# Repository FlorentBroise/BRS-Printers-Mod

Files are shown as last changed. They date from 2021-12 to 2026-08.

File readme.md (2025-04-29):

# Welcome to the BRS-Engineering printers upgrades project!


**What is done here?**  The main objective here is to develop relevants upgrades to push the 3D printer to the limit we choose to, especially repetability and high precision quality goals in mind. You will find some manuals, procedures and tips!
Here a lot of premium upgrades for the Vcore3, with a lot of capabilities. Either you can make it yourself, I offer a print service at https://store.brs-engineering.com specialize in PACF materials if needed. Happy browsing!

# Vcore 3.0/3.1/4.0 based
## Quick Navigation

Chapter|Content Description
:---: |-------------------
Intro.|[What is done here?](/intro.md)
1.|[Define what you need](/defineneeds.md)
2.|[Frame](/frame.md)
3.|[General Upgrades and options (Z-Upgrade, AWD,...)](/componentselection.md)
4.|[BOM](/purchased.md)
5.|[L3VER Tensionner / Enclosure Plates / Prototypes](/products.md)
6.|[Assembly Instructions](/assembly.md)
7.|[Klipper Setup](/Klipper/start-table.md)
8.|[Calibration](/calibration.md)
9.|[Procedures](/procedures.md)
10.|[Cura tips](/software.md)
11.|[EVA Mods](/evamods.md)
12.|[VZ Mods](/vzmods.md)
13.|[Spool system)](/options.md)
14.|[How to Print your Parts](/howtoprint.md)
15.|[LEGACY/DEPRECATED](/deprecated.md)
16.|[Usefull links](/links.md)
17.|[Credits](/credits.md)
18.|[CAD changelogs](/changelogs.md)

# BRS-Vulcain I
## Quick Navigation
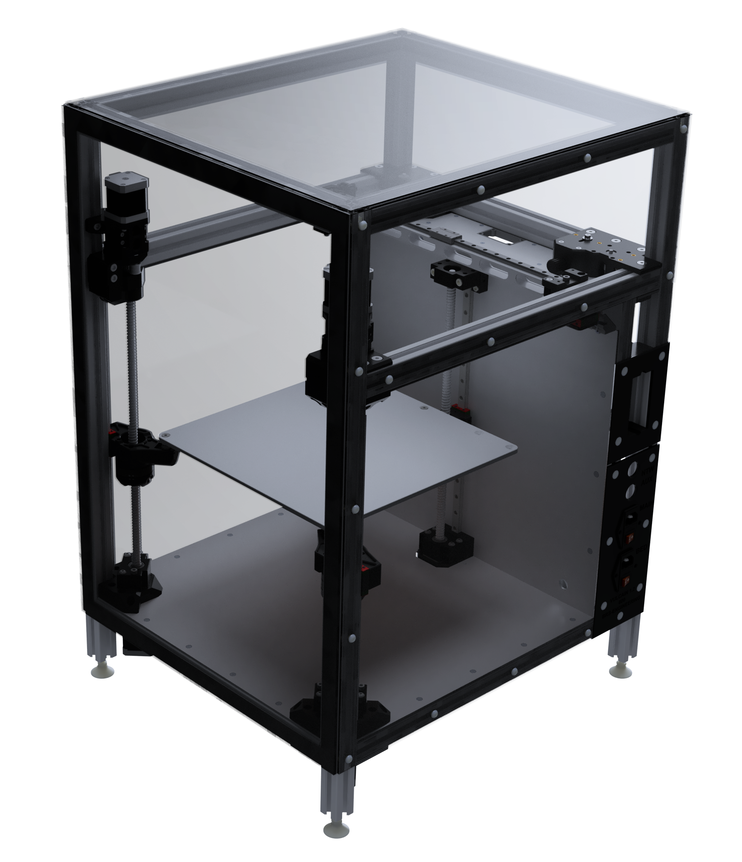
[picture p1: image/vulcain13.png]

Chapter|Content Description
 :---: |-------------------
Intro.|[What is it?](/intro1.md)
1.|[Frame](/frame.md)
2.|[CAD](cad/VULACIN-1.3/Vulcain.md) AVAILABLE

# Licenses

Most projects and designs are licensed as
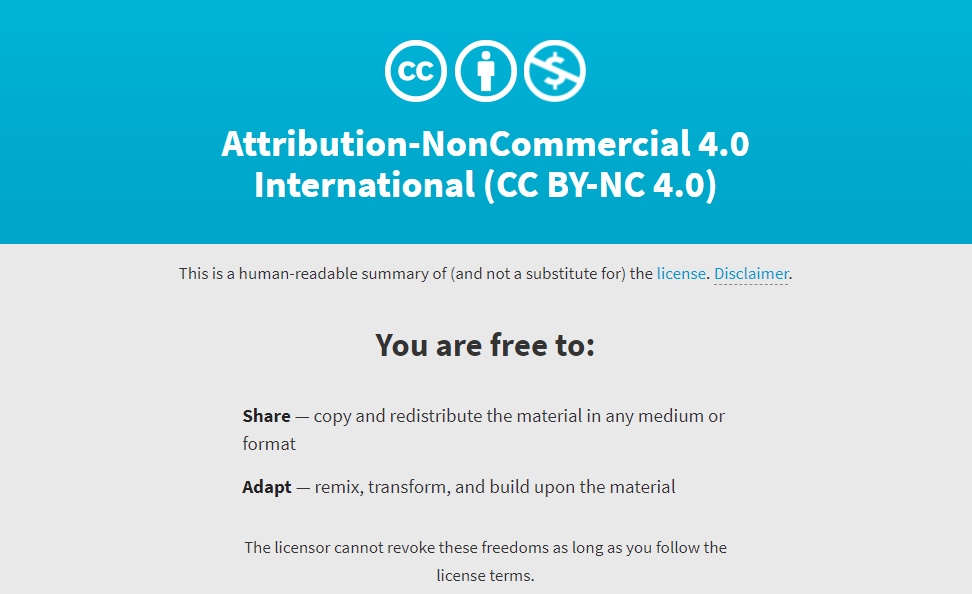
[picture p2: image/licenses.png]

For others, the licence and attribution will be displayed

Feel free to ask if you want to sell it yourself

# Donation

If you like my work and would like to help me covering the costs associated to the development of prototypes and improvements of every projects, my company is a little french one man handed thing ;) <br>
click the button here below :)
[Paypal Donation](https://www.paypal.com/donate/?hosted_button_id=VEMAB3WH74FW2)

# Links

Official Website: https://www.brs-engineering.com/
Official Store: https://store.brs-engineering.com/
Facebook pages: https://www.facebook.com/FlorentBroiseEngineering
Youtube: https://www.youtube.com/channel/UCkiClJtaGl32GyRtkntkpkw

Thank you!
Florent Broise

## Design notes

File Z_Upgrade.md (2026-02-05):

## -/ Z SYSTEM 3.0 (For Vcore 4)

# -/ Z-Upgrade 1204/1605 4.0

A Z-Upgrade complete overhaul for VCORE 4.0/4.1
The Z-Upgrade replace the original Z system with a ballscrews driven system.
More precise, more reliable over time, it offers a very high repeatability and a perfect consistancy in layer staking compared to a trapezoidal screw.
Maintenance-free and made to last in a production line. No wobble over Z.
Proofed design since 2021. More than 450+ happy users

Lifetime support and warranty over the parts

Integrated design pushed further to maximize fonctions and size to keep the whole print Z volume
Following the feedbacks, tests, assemblies, this version is born to simplify, and solve all the little things from the 3.x versions.
Parts count reduced, hardware quantity reduced, steps of assembly reduced, price reduced!

Version|Description|ReleaseDate|CAD|Printable|BOM|Documentation|License|Order
-------------|-----------|-----------|-----------|------------|------------|----------|-----------|-----------
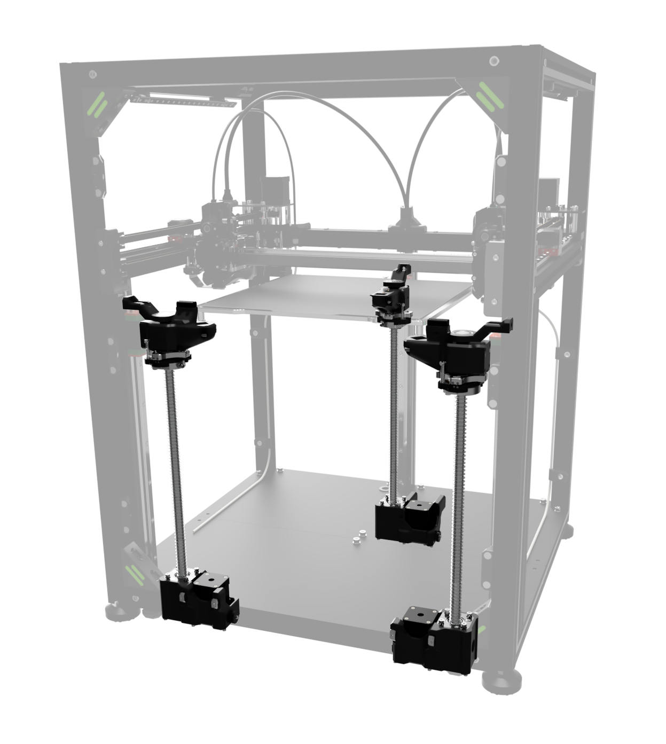
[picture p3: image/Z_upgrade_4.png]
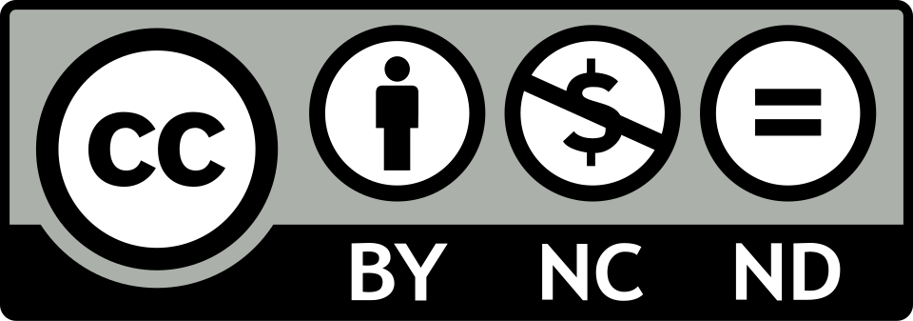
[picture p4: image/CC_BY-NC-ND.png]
**V4.0a 1605 ACTIVE|<br>SFU1605 Version - Release |01/02/26| > | [Files](https://www.printables.com/model/1577140-z-upgrade-40-for-vcore-4041)| [BOM](https://docs.google.com/spreadsheets/d/1dxGWueJq1Y-2fWoLZl0RPUSDvyyU8gKnJiP1dbby-7s/edit?usp=sharing) | [MANUAL](/manuals/Z-Upgrade-4.0-Manual.pdf) || [SHOP on the Store](https://store.brs-engineering.com/products/z-upgrade-4-0-for-vcore-4-0-4-1)

# -/ Z-Upgrade 1204/1605 3.0

Adaptation of the production grade "Z-Upgrade" for VCORE 4.0
Upgrade to replace the original Z with a ballscrew system.
More precise, very reliable over time, offers a very high repeatability in the Z movement compared to a trapezoidal screw.
Maintenance-free*. Made to last in a production line. No wobble over Z. Proofed design over 2021. More than 350+ users since 2021.
A Reinforced version of the 1605 is available too for heavy duty projects. This system has virtually no Z limitations in size, you can dream of the best you can pick ;)

A lot of things has been reworked on this iteration compare to the previous Z-Upgrade 2.0:

-Simplification of parts list, easier implementation. direct bolt in upgrade.

-Directly bolted to the VCORE 4.0 frame and underplate. Re-use the Stock VC4 top retainers (1204 version) + bearings.

-No need of surelevation; the Stock VC4 feet will only need to be adjusted to the height. (+17mm)

-Compatible natively with Wobble X, Oldham V3 proofed printed rings compatible too

-Dense integration of the Oldham/Wobble X in the Arms

-Motor reduction for a very high holding torque, even when the motor aren't active. Proofed for heavy custom bed, or bigger custom print volume machines. Vcore 500 can now run standard Nema 17 without risks of fall when the motor are powered off

-Motor reduction + ballscrew allowing an insane precision over the Z-Motion, extreme constistency, allow thin and repetable layer over time

-No maintenance needed (cleaning+thin lubrication once a year is enough)

-Z-motors easy tension over the 6mm timing belt with 1x M5 screw

-Add +10mm of Z distance (Oldham V3), or +15mm with Wobble X

-All included, no self soucing to do.

[GUIDE TO CHOOSE and PATCH NOTE](https://github.com/FlorentBroise/BRS-Printers-Mod/blob/main/manuals/Z-Upgrade-3.2C-Variants.pdf)

Version|Description|ReleaseDate|CAD|Printable|BOM|Documentation|License|Order
-------------|-----------|-----------|-----------|------------|------------|----------|-----------|-----------
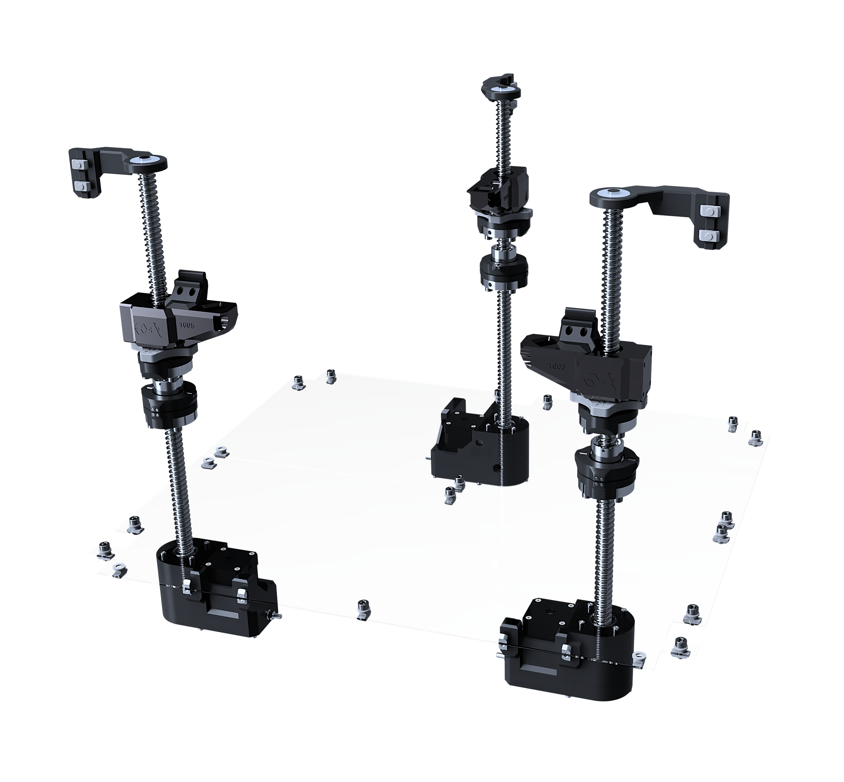
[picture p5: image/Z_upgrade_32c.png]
**V3.0a 1204 DEPRECATED|<br>SFU1204 Version - This version is made to simplify the integration to a stock VCORE 4 (All versions), By taking the same footprint that the stock VCORE 4 parts. You can then use the stock bottom panel you already have, and (PRECISE BOM listed bellow). NO NEED for clearance bellow the frame, tuning the stock Z feet height is enough!. This version keep the same Z volume (+10-15mm bonus) than the stock machine|30/04/24| > |  | [BOM](https://docs.google.com/spreadsheets/d/1E3s1GYlrxwITHgYWx6jKaRsaI9jWW35iHJ5XEkeNflE/edit?gid=0#gid=0) | [MANUAL](/manuals/Z-Upgrade-3.0-Manual-1.0.pdf) ||/
**V3.1a/b 1204 DEPRECATED|<br>SFU1204 + SFU1605 added. - This version is made to implement 1605 version (b) and to change all bottop plate screws to m3x20mm to simplify sourcing|12/11/24| > |  | [BOM](https://docs.google.com/spreadsheets/d/1E3s1GYlrxwITHgYWx6jKaRsaI9jWW35iHJ5XEkeNflE/edit?gid=0#gid=0) | [MANUAL](/manuals/Z-Upgrade-3.0-Manual-1.0.pdf) ||/
**V3.2c 1204/1605 DEPRECATED|<br>SFU1605/SFU1204 Version - This version is made to simplify the production and manufacturing on the BRS side, it merges the 1605 and 1204 designs to count less parts, StarLock design created, some adjustments made on the general design [Z-Upgrade 3.2 PATCHNOTE.pdf](https://github.com/user-attachments/files/17843025/Z-Upgrade.3.2.PATCHNOTE.pdf)|21/01/25| > | [1605 STL-STEP-F3z](https://www.printables.com/model/1033344-z-upgrade-32-for-vcore-40-sfu1605-sfu1204) [1204 STL-STEP-F3z](https://www.printables.com/model/1419210-z-upgrade-32d-sfu1204-arm-kit) | [BOM](https://docs.google.com/spreadsheets/d/1E3s1GYlrxwITHgYWx6jKaRsaI9jWW35iHJ5XEkeNflE/edit?gid=0#gid=0) | [MANUAL](/manuals/Z-Upgrade-3.0-Manual-1.0.pdf) ||[SHOP ](https://store.brs-engineering.com/products/z-upgrade-3-0-sfu1605-vcore-4-0)
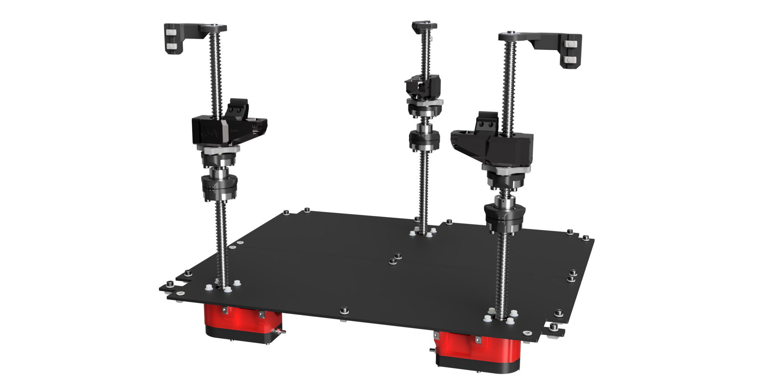
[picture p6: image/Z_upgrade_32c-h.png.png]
**V3.2c-H 1605 ADEPRECATED|<br>SFU1605 Version - This is the Z-Upgrade 3.2C-H iteration (H, for heavy), It answers the need to make a very tall printer (800-1500mm)|17/03/25| > | [STL-STEP-F3z](https://www.printables.com/model/1233695-z-upgrade-32c-h-for-tall-vcore-40-sfu1605) | BOM In progress | [MANUAL](/manuals/Z-Upgrade-3.0-Manual-1.0.pdf) ||[SHOP ](https://store.brs-engineering.com/products/z-upgrade-3-2c-sfu1605-reinforcedvcore-4-0)
**V3.2d 1204/1605 DEPRECATED|<br>SFU1605/SFU1204 Version - Upgrade or the arm design with retaining spings to secure the wobble assembly na dprevent accident or ball bearing drops [Z-Upgrade 3.2d PATCHNOTE.pdf]() Soon |16/06/25| > | [STL-STEP-F3z](https://www.printables.com/model/1033344-z-upgrade-32-for-vcore-40-sfu1605-sfu1204) | [BOM](https://docs.google.com/spreadsheets/d/1E3s1GYlrxwITHgYWx6jKaRsaI9jWW35iHJ5XEkeNflE/edit?gid=0#gid=0) | [MANUAL](/manuals/Z-Upgrade-3.0-Manual-1.0.pdf) ||[SHOP ](https://store.brs-engineering.com/products/z-upgrade-3-0-sfu1605-vcore-4-0)
**V3.2d-H 1605 DEPRECATED|<br>SFU1605 Version - This is the Z-Upgrade 3.2d-H iteration (H, for heavy), It answers the need to make a very tall printer (800-1500mm) Upgrade or the arm design with retaining spings to secure the wobble assembly and prevent accidents or ball bearing drops|16/06/25| > | [STL-STEP-F3z](https://www.printables.com/model/1233695-z-upgrade-32c-h-for-tall-vcore-40-sfu1605) | BOM In progress | [MANUAL](/manuals/Z-Upgrade-3.0-Manual-1.0.pdf) ||[SHOP ](https://store.brs-engineering.com/products/z-upgrade-3-2c-sfu1605-reinforcedvcore-4-0)

## -/ Creative Commons known infringment to the model

Version|Description|Release Date of the illegal copy|CC infringment|Origin|Documentation|License|Action taken
-------------|-----------|-----------|-----------|------------|------------|----------|-----------
**V3.x|<br>SFU1605 Version Copy-paste product |+-June 2025| YES - BY no credits and NC comercial usage | PRINT BIG (Core AM GmBh) | [Demonstration](/image/PB-CC-ZU3x.pdf) |  | PRINT BIG refuse to comply to the CC yet, no further action taken yet

## -/ Z SYSTEM 2.0 (For Vcore 3.0/3.1)

# -/ Z SYSTEM 1204 2.8DE (For Vcore 3.0/3.1)

- Z-Ballscrews-upgrade 2.8 LAST AND DEFINITIVE REVISION
High precision Z system with anti-wobble system

Avantages:
-Easy installation over a Stock 3.1
-Increase Z repetability
-Lower maintenance, no wear like the TR8 LS/nut
-High precision accuracy over time, made to last in a production line.
-No wobble over Z
-Proofed design over 2021. More than 350+ users since 2021. Lifetime Support
-Easy implementation to any Vcore, use the same bottom pannel patern than stock

Version|Description|ReleaseDate|CAD|Printable|BOM|Documentation|License|Order
-------------|-----------|-----------|-----------|------------|------------|----------|-----------|-----------
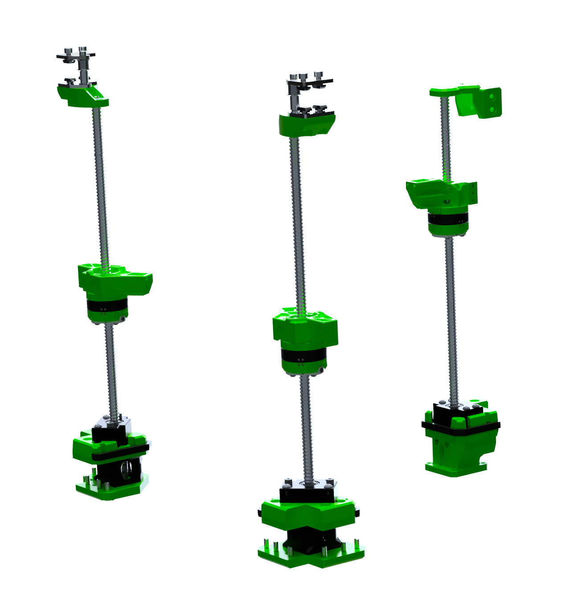
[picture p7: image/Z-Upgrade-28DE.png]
**V2.8a 1204|<br>SFU1204 Version - Last revision of the Z-Upgrade 2.0, This version is made to simplify the integration to a stock VCORE 3.1 (All versions), By taking the same footprint that the stock VCORE 3.1 parts. You can then use the stock bottom panel you already have, and recycle the stock screws list to limit an extended new selfsourcing process; you will need to source some additionnal screws (PRECISE BOM listed bellow). Need a clearance bellows the frame, the use of 70mm feets will be mandatory. This version keep the same Z volume than the stock machine, no more Z reduction!|11/02/24| [STEP](https://github.com/FlorentBroise/BRS-Printers-Mod/blob/main/cad/Z-upgrade-28-DE.zip) | [STL](https://www.printables.com/model/763486-z-upgrade-28-definitive-edition) | [BOM](https://docs.google.com/spreadsheets/d/1hA8UdFV7IhUFEDgt_LVLpt3l6aZIOX_8x9tYVwdvjZA/edit?usp=sharing) | [MANUAL](https://github.com/FlorentBroise/BRS-Printers-Mod/blob/main/manuals/manual2EN.pdf) ||[SHOP](https://store.brs-engineering.com/products/z-upgrade-2-0-vcore-3-x)
# -/ Z SYSTEM 1605 2.8DE (For Vcore 3.0/3.1)
The last Z-Upgrade 1605 version stopped at 2.8DE revision.

Avantages:
-Easy installation over a Stock 3.1
-Increase Z repetability
-Lower maintenance, no wear like the TR8 LS/nut
-High precision accuracy over time, made to last in a production line.
-No wobble over Z
-Proofed design over 2021. More than 350+ users since 2021. Lifetime Support
-For CUSTOM long size machines, can be scale to insane lenghts

Version|Description|ReleaseDate|CAD|Printable|BOM|Documentation|License|Order
-------------|-----------|-----------|-----------|------------|------------|----------|-----------|-----------
**V2.8b Heavy Duty 1605 EXTENDED|<br>SFU0605 Version - Last revision of the Z-Upgrade 2.8 1605, |22/08/24| [STEP](https://www.printables.com/model/982028-z-upgrade-28c-definitive-edition-1605-brs-oldham) | | | [MANUAL](https://github.com/FlorentBroise/BRS-Printers-Mod/blob/main/manuals/manual2EN.pdf) ||[SHOP](https://store.brs-engineering.com/products/z-upgrade-2-0-vcore-3-x)

# -/ Z SYSTEM 1605 2.7 (For Vcore 3.0/3.1)(Deprecated for 2.8b DE)
The last Z-Upgrade 1605 version stopped at 2.1 revision.

Avantages:
-Easy installation over a Stock 3.1
-Increase Z repetability
-Lower maintenance, no wear like the TR8 LS/nut
-High precision accuracy over time, made to last in a production line.
-No wobble over Z
-Proofed design over 2021. More than 350+ users since 2021. Lifetime Support
-For CUSTOM long size machines, can be scale to insane lenghts

Version|Description|ReleaseDate|CAD|Printable|BOM|Documentation|License|Order
-------------|-----------|-----------|-----------|------------|------------|----------|-----------|-----------
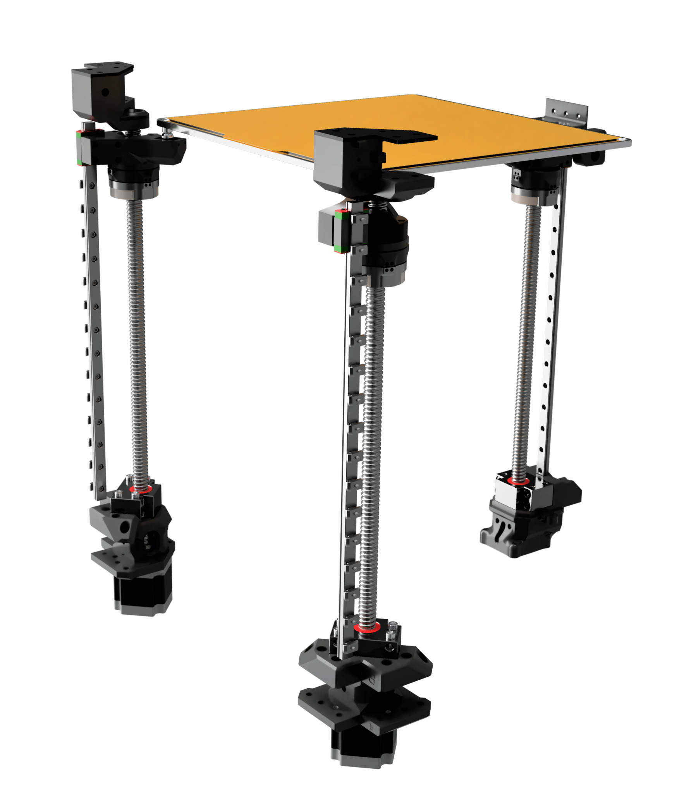
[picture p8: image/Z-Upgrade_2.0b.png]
**V2.1b Heavy Duty 1605 EXTENDED|<br>SFU0605 Version - Last revision of the Z-Upgrade 2.0 1605, some correction of the offsets have been made|13/03/24| [STEP](https://github.com/FlorentBroise/BRS-Printers-Mod/raw/main/cad/ZU20b-1605.zip) | | | [MANUAL](https://github.com/FlorentBroise/BRS-Printers-Mod/blob/main/manuals/manual2EN.pdf) ||[SHOP](https://store.brs-engineering.com/products/z-upgrade-2-0-vcore-3-x)

Credits: 

-@Ratrig for the VCORE-3.0/3.1/4.0 amazing design

-@MirageC / EVOMOTO Oldham/Wobblex magical design

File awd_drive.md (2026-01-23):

## -/ BRS-AWD Drives for VC4.0

Based on the "best seller" product of BRS-ENGINEERING, the BRS-AWD for Vcore 3/3.1, I present you the BRS-AWD V2, exclusively made for the VCORE 4.0.

Why this mod? The VC4 get the Hybrid layout...
Well most people are focused on the single toolhead setup, Hybrid CoreXY is focused for IDEX layouts. Here the BRS-AWD V2 will unlock some cool specs:

-Way less complex than the Hybrid layout: you keep only the 2 CoreXY belts (XY), no need to add 2 others for Y. This give you less parts, less variables, leading to a better reliability, a better calibration, and way less maintenance. Beside that, the system is more balanced.
-On the performance side, no need to proove AWD layouts legendary performances, it improves single toolhead acceleration, speed, but more importantly the print quality
-Easy assembly, no modifications of the Frame needed, no need of Enclosure modifications. Require at least 30-60mm more belt lenght
-Integrated brand new coaxial belt tensionner
-The more dense mechanism made on any BRS upgrade so far for a small form factor&nbsp;

AWD mod to add to a CoreXY Vcore 4.0, easy and reliable AWD configuration
- Abec-5/7 bearing for an increased lifespan

Version|Description|ReleaseDate|CAD|BOM|Documentation|Printable-STL|License|Order
-------------|-----------|-----------|------------|------------|------------|------------|-----------|-----------
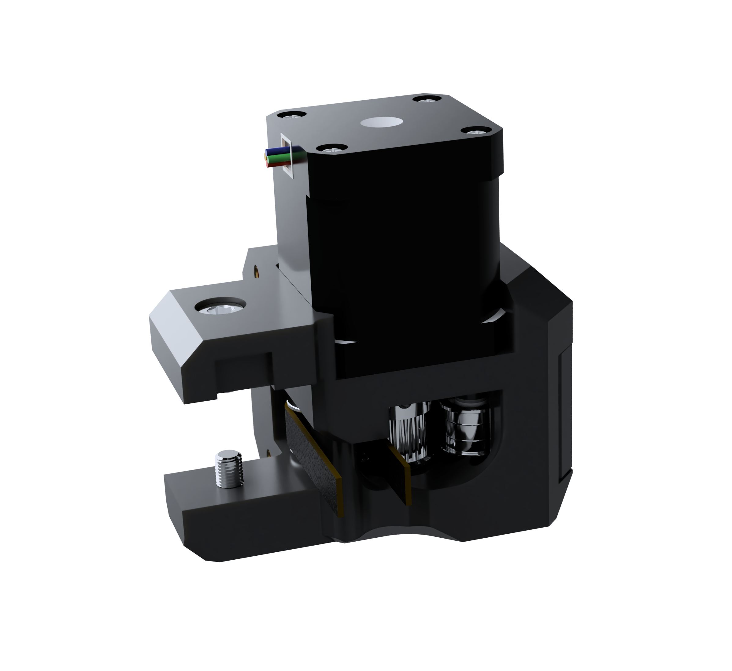
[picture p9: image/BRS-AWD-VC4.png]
**V2.0 COREXY VC4.0**|<br> Release|29/04/25|[STEP](https://www.printables.com/model/1293006-brs-awd-v20-vcore-40)|[BOM]cf Manual|[Manual](manuals/BRS_AWD_Drive_2.0_VC4.pdf)/ [Klipper-CFG]cf Manual| [STL Files](https://www.printables.com/model/1293006-brs-awd-v20-vcore-40)||[SHOP](https://store.brs-engineering.com/products/brs-awd-drive-v2-full-kit)
**V2.1 COREXY VC4.0 + VC3.0/3.1**|<br> Works for All VCORE machines|30/9/25|[STEP](https://www.printables.com/model/1293006-brs-awd-v20-vcore-40)|[BOM]cf Manual|[Manual](manuals/BRS_AWD_Drive_2.0_VC4.pdf)/ [Klipper-CFG]cf Manual| [STL Files](https://www.printables.com/model/1293006-brs-awd-v20-vcore-40)||[SHOP](https://store.brs-engineering.com/products/brs-awd-drive-v2-full-kit)
**V2.2 COREXY VC4.0/4.1 + VC3.0/3.1**|<br> Works for All VCORE machines|01/01/26|[STEP](https://www.printables.com/model/1293006-brs-awd-v20-vcore-40)|[BOM]cf Manual|[Manual](manuals/BRS_AWD_Drive_2.0_VC4.pdf)/ [Klipper-CFG]cf Manual| [STL Files](https://www.printables.com/model/1293006-brs-awd-v20-vcore-40)||[SHOP](https://store.brs-engineering.com/products/brs-awd-drive-v2-full-kit)

|[SHOP](https://store.brs-engineering.com/products/brs-awd-drive-v2-full-kit)

## -/ BRS-AWD Drives for VC3.0 and VC3.1

- AWD mod to add ANY Vcore version an easy and reliable AWD configuration
- Drive are mounted on a damper system, reducing noised. Pulleys mounted on steeshft and secured with Abec-5/7 bearing for an increased lifespan
- Easy assembly, no modifications of the Frame needed, no need of Enclosure modifications. Require at least 30-60mm more belt lenght
- COMPATIBLE WITH: Vcore 3.0, Vcore 3.1, 200mm 300mm 400mm 500mm and more, Opened or closed front, Enclosure 1.0 (VC3.0), Extended Enclosure 2.0 (V3.1), Stock Z leadsrews, MBFS Ventermech, BRS Ballscrews Z-upgrade 1.0 and 2.0 with SFU1204 and 1605 (incoming), works better with the L3VER M2, compatible with any versions of the L3ver M1
- BE AWARE that in order to work with L3ver M2 modules, you need to get ther M2 it mirrored to match the 45° X-Y-X1-Y1 motor positions
- Bearing and Pulleys has 1mm variation on position between the VC3.0 and VC3.1 version to perfectly align the 3.0/3.1 belt path variations
- MORE DETAILS AND PICTURES [HERE](https://store.brs-engineering.com/products/brs-awd-drive-1-1)

Version|Description|ReleaseDate|CAD|BOM|Documentation|Printable-STL|License|Order
-------------|-----------|-----------|------------|------------|------------|------------|-----------|-----------
**V1.1**|First release. |19/08/23|||||||
**V1.2**|First revision; some notches has been added to ease of assembly for the NEMA M3x20 underscrew. |27/08/23||||||
**V1.3**|FIX SFU1204 adaptation; Some offsets applied and simplification for the assembly |27/08/23||||||
**V1.31**|FIX SFU1204 adaptation; Some offsets applied and simplification for the assembly |27/08/23||||||
**V1.32**| FIX an little misalignment for stock VC3.1 underplates |04/09/23||||||
**V1.34 VC3.1 for Z-Upgrade SFU1605 **|<br> CAD Layout mofification, 1 STEP file for each Variation. Replacment of the 2x top M6x12 by countersunk version for the 1.0 Enclosure. FIX of a the spindle bearing alignment |01/10/23|[STEP 3.1 1605](cad/BRS-AWD-Drive-31-SFU16051.33.zip)||[Manual](manuals/BRS-AWD-Drive-V135a.pdf) / [Klipper-CFG](https://github.com/FlorentBroise/BRS-Printers-Mod/tree/main/manuals/KlipperconfAWD.cfg)|[STL Files](https://www.printables.com/model/557508-brs-awd-drive-v134-for-vcore-3031) ||[SHOP](https://store.brs-engineering.com/products/brs-awd-drive-1-1)
**V1.34 Stock VC3.1**| DEPRECATED <br> CAD Layout mofification, 1 STEP file for each Variation. Replacment of the 2x top M6x12 by countersunk version for the 1.0 Enclosure |27/09/23|[STEP 3.1 Stock](cad/BRS-AWD-Drive-31-Stock_.step)||[Manual](manuals/BRS-AWD-Drive-V135a.pdf) / [Klipper-CFG](https://github.com/FlorentBroise/BRS-Printers-Mod/tree/main/manuals/KlipperconfAWD.cfg)| [STL Files](https://www.printables.com/model/557508-brs-awd-drive-v134-for-vcore-3031)||[SHOP](https://store.brs-engineering.com/products/brs-awd-drive-1-1)
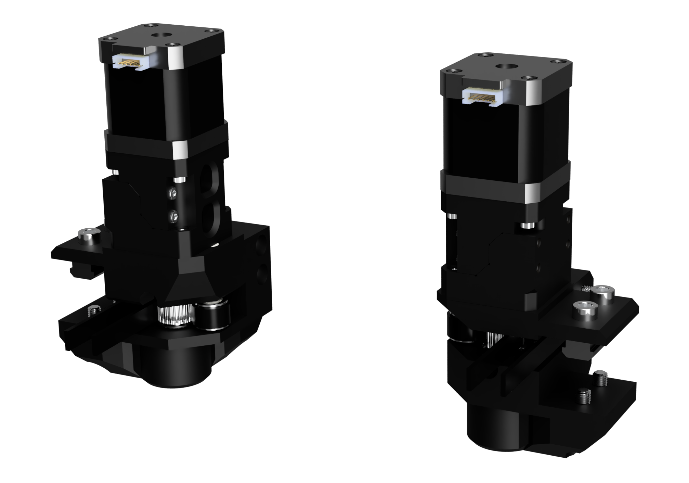
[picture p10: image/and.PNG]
**V1.34 VC3.1 for Z-Upgrade SFU1204 (1.0/2.0)**|<br> CAD Layout mofification, 1 STEP file for each Variation. Replacment of the 2x top M6x12 by countersunk version for the 1.0 Enclosure. FIX of a the spindle bearing alignment |27/09/23|[STEP 3.1 1204](cad/BRS-AWD-DRIVES-31-SFU1204.zip)||[Manual](manuals/BRS-AWD-Drive-V135a.pdf) /[Klipper-CFG](https://github.com/FlorentBroise/BRS-Printers-Mod/tree/main/manuals/KlipperconfAWD.cfg)|[STL Files](https://www.printables.com/model/557508-brs-awd-drive-v134-for-vcore-3031) ||[SHOP](https://store.brs-engineering.com/products/brs-awd-drive-1-1)
**V1.35a VC3.1 for Z-Upgrade SFU1605 **|   BRS-AWD_Drive_31_SFU1605_v4_2024-Mar-12_02-14-55AM-000_CustomizedView2091081567<br> CAD Layout mofification, 1 STEP file for each Variation. Replacment of the 2x top M6x12 by countersunk version for the 1.0 Enclosure. FIX of a the spindle bearing alignment |12/03/24|[STEP 3.1 1605](cad/BRS-AWD-Drive-31-SFU1605135.zip)||[Manual](manuals/BRS-AWD-Drive-V135a.pdf) / [Klipper-CFG](https://github.com/FlorentBroise/BRS-Printers-Mod/tree/main/manuals/KlipperconfAWD.cfg)|[STL Files](https://www.printables.com/model/557508-brs-awd-drive-v134-for-vcore-3031) ||[SHOP](https://store.brs-engineering.com/products/brs-awd-drive-1-1)
**V1.35a Stock VC3.1**|BRS-AWD-Drive-31-Stock__2024-Mar-12_02-20-16AM-000_CustomizedView13298513461<br> Some design change to reduce print volume and design simplicication. Add a 4th m3x30 to a better motorblock anchor |20/11/23|[STEP 3.1 Stock Open + Close](cad/BRS-AWD-Drive-31-Stock-135a.zip)|[BOM](https://docs.google.com/spreadsheets/d/1lZiieI_m1PFYK_gN3xTSUbtMcLak3CRZo3O83WT3AfU/edit?usp=sharing)|[Manual](manuals/BRS-AWD-Drive-V135a.pdf) / [Klipper-CFG](https://github.com/FlorentBroise/BRS-Printers-Mod/tree/main/manuals/KlipperconfAWD.cfg)| [STL Files](https://www.printables.com/model/557508-brs-awd-drive-v135a-for-vcore-3031)||[SHOP](https://store.brs-engineering.com/products/brs-awd-drive-1-1)
**V2.2 COREXY VC4.0/4.1 + VC3.0/3.1**|<br> Works for All VCORE machines|01/01/26|[STEP](https://www.printables.com/model/1293006-brs-awd-v20-vcore-40)|[BOM]cf Manual|[Manual](manuals/BRS_AWD_Drive_2.0_VC4.pdf)/ [Klipper-CFG]cf Manual| [STL Files](https://www.printables.com/model/1293006-brs-awd-v20-vcore-40)||[SHOP](https://store.brs-engineering.com/products/brs-awd-drive-v2-full-kit)

## -/ Option for BRS-AWD Drives
- AWD mod to add ANY Vcore version an easy and reliable AWD configuration

Version|Description|ReleaseDate|CAD|Printable|BOM|Documentation|License|Order
-------------|-----------|-----------|-----------|------------|------------|------------|-----------|-----------
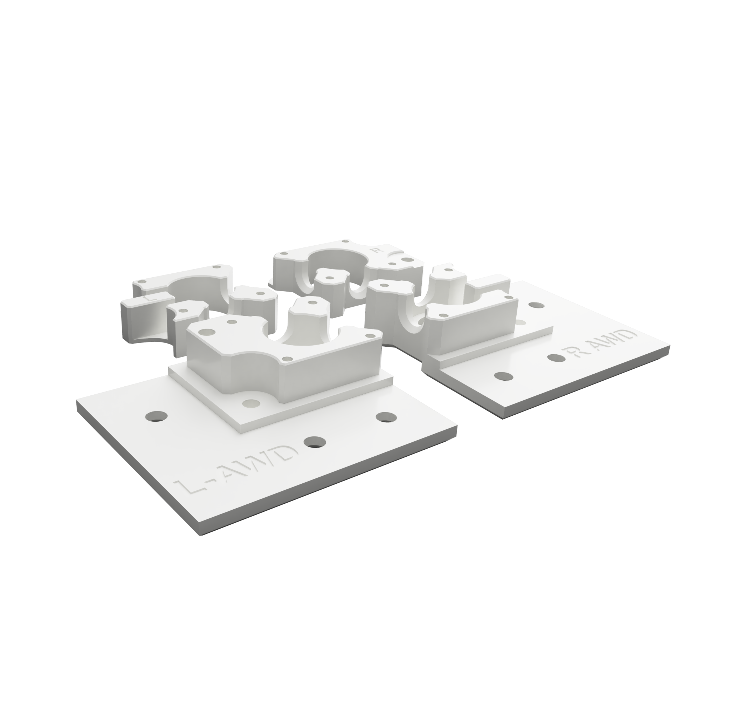
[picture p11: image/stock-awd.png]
**V1.0 VC3.1 Mirrored Rear blocks for AWD**|<br>Mirrored rear Stock plates to use the BRS-AWD correctly |04/10/23|[STEP](cad/BRS-AWD-stock.step)| [STL](https://www.printables.com/model/616219-vcore-31-stock-rear-block-mirrored/files)||[Manual](manuals/BRS-AWD-Drive-v132.pdf) ||[SHOP](https://store.brs-engineering.com/products/brs-awd-drive-1-1)

Special credit to @AJES! / Anders Velling Jorgensen

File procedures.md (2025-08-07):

# BRS-Engineering  
## Procedure

In this section you will find manuals for all upgrades. 

Topic|Status|View|Procedure|Calculations sheet
-----------------|------|-----------------------------------| :---------------: | :---------------:
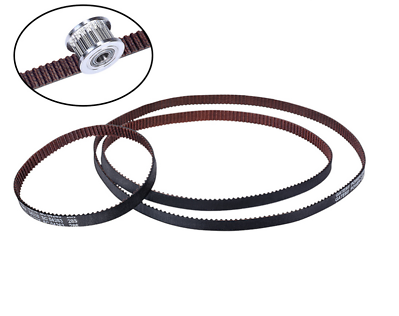
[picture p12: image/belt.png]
BELT TENSION | Active| <br> **Belt tension procedure** | [Download](/manuals/belt.pdf) | [Download](/manuals/Belt_Tension_Calculations.ods)
GANTRY PLANE LASER LEVEL | Active| <br> **Gantry plane laser-level procedure** | [Download](/manuals/Gantry-plane-level.pdf) | /

## [Back to Main Page](/README.md)

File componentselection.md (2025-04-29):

# Upgrades

#The shop has moved to https://store.brs-engineering.com/

#SEE THE SUBSECTION ON THE LAST PAGE TO FIND YOUR NEEDS ;)

|Subsection|Content Description
 |:---: |-------------------
| A |[Z Upgrade for VCore](/Z_Upgrade.md)
| B |[Gantry](/Gantry.md)
| C |[Toolheads](/Toolheads.md)
| D |[BRS-AWD Drive](/awd_drive.md)
| E |[Air quality / Filtration](/Air-Filtration.md)
| F |[Various plates](/Plates-Enclosures.md)
|G |[Specific Products (L3VER/IDEX/Proto)](/products.md)

# Credits: 
Here few people/Companies who I want to thank, for inspiring reasons, constructive discussions, engineering skills, work and vision in general. Consider looking in their work, and donate to support their constant effort by pushing 3D printing forward:

-Olivier Royer-Tardif / MirageC [Hevort project](https://miragec79.github.io/HevORT/)

-Simon Vez [VzBot](https://github.com/VzBoT3D/VzBoT-Vz330)

-Jerôme Wiedemann [RomRider](https://github.com/RomRider)

-Pawel Kucmus [EVA](https://main.eva-3d.page/)

-Keegan Wentz (Wentz-dynamics)

-Oleg Ok [EvoMotors](https://www.thingiverse.com/evomotors/designs) 

-RatRig Team [Page](https://ratrig.com/v-core3default.html)

-Fabreeko / Honey Badger [Page](https://www.fabreeko.com/collections/fabreeko)

-AJES! / Anders Velling Jorgensen 

More extensive credit can be found here: https://www.brs-engineering.com https://www.brs-engineering.com/Oldham.html

[Back to Main Page](/readme.md)

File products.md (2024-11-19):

# BRS-Engineering  
## Specific Products (L3VER tensionner / Enclosure Plates / Prototypes)

In this section you will find specific products, not shared on the regular CAD side. It can be bought at BRS Shop. As prototyping is time hungry and expensive, this is a mean for you to participate further in the next developments ;)

## L3VER M3 AWD TENSIONNER 
The M3 replace the front idlers blocks, adding tensionner and AWD feature in one part and in a low profile

Product|Status|View|Manual EN| STL+STEP | Release date|Shop Product| More|License
-----------------|------|-----------------------------------| :----: |  :---------------: |  :---------------: |  :---------------: | :---------------: | :---------------:
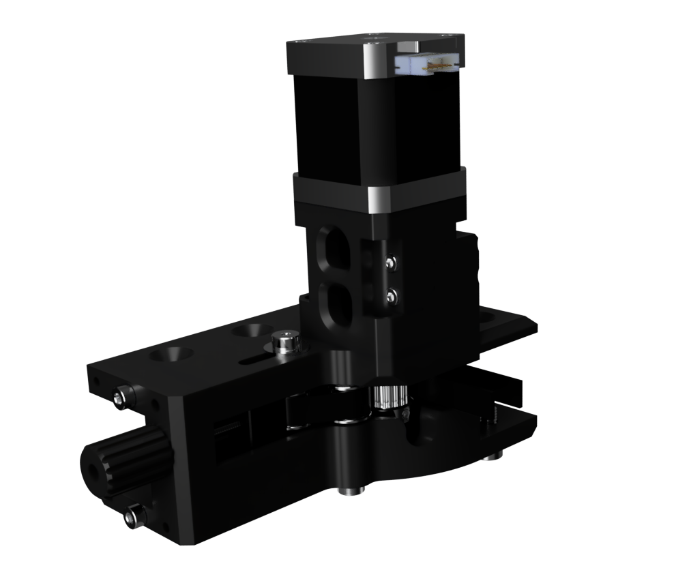
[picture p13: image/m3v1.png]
AWD301/1 Drive with L3VER M3 Tensionner module|ACTIVE|<br> **FOR VCORE3.0/3.1 with 1.0 Enclosure** AWD and belt tensionner module all in one, Only for VC3.0/3.1 with stock frame or enclosure 1.0 | [BOM](https://docs.google.com/spreadsheets/d/1m4azE54TQerhyBI3S39cNwWqPLjUHiSjp3UHa-RHm1U/edit?usp=sharing)  Manual incoming | [STEP](https://www.printables.com/model/860203-l3ver-m3-awd-combo-vcore-3031-for-enclosure-10) [STLs](https://www.printables.com/model/860203-l3ver-m3-awd-combo-vcore-3031-for-enclosure-10)|02/04/24|[SHOP](https://store.brs-engineering.com/products/l3ver-m3-awd-module)|[CAD](https://www.printables.com/model/860203-l3ver-m3-awd-combo-vcore-3031-for-enclosure-10)| 
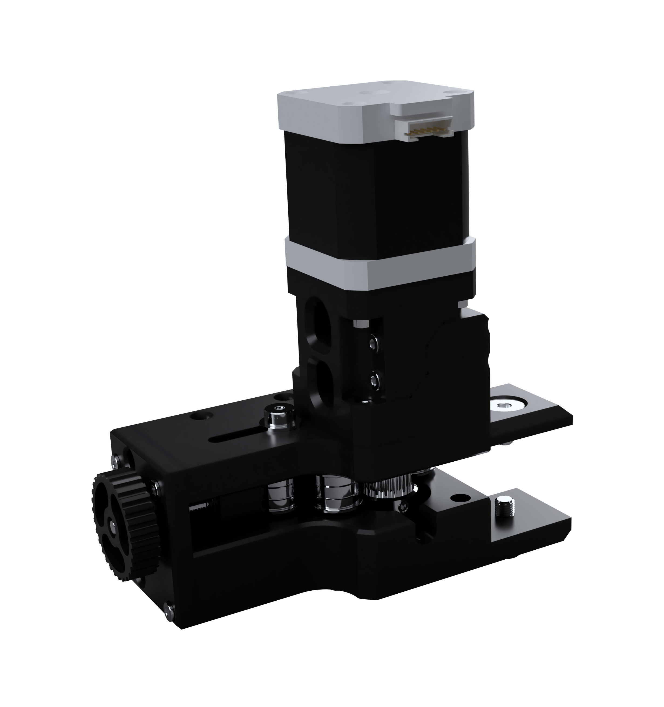
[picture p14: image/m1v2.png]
AWD301/2 Drive with L3VER M3 Tensionner module|ACTIVE|<br> **FOR VCORE3.0/3.1 with 2.0 Enclosure** AWD and belt tensionner module all in one, Only for VC3.0/3.1 with stock frame or enclosure 2.0 |[BOM](https://docs.google.com/spreadsheets/d/1Q-RR1Z1-t3DGIQ9Xbndv41vbUf74H0XFt3EJaa1Jg0M/edit?usp=sharing) , Manual incoming | [STEP](https://www.printables.com/model/860767-l3ver-m3-awd-combo-vcore-3031-enclosure-20) [STLs](https://www.printables.com/model/860767-l3ver-m3-awd-combo-vcore-3031-enclosure-20)|28/04/24|[SHOP](https://store.brs-engineering.com/products/l3ver-m3-awd-module)|[CAD](https://www.printables.com/model/860767-l3ver-m3-awd-combo-vcore-3031-enclosure-20)| 

### L3VER M1 TENSIONNER (3.0 / 3.1)
IF you dont want to change the motor bracket, (very simple installation) Good for already working machines

Product|Status|View|Manual EN|Release date|Shop Product |Shop CAD|License
-----------------|------|-----------------------------------| :----: |  :---------------: |  :---------------: |  :---------------: |  :---------------:
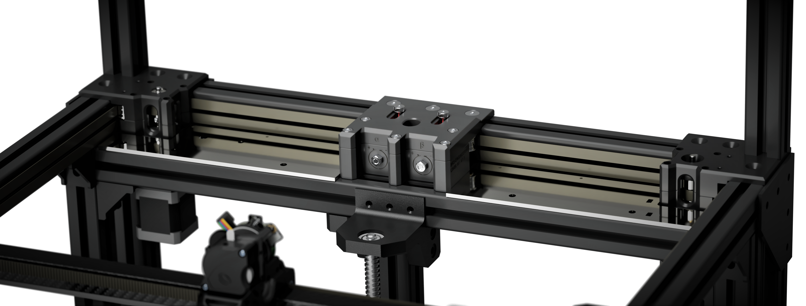
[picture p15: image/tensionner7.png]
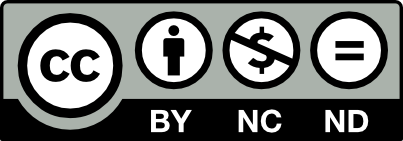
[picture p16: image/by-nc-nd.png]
L3VER M1 1.0 (A1.1) Tensionner module|Active|<br> **L3VER M1 1.0 A1 Tensionner** A full Vcore 3 compatible manual tensionner block removing the need of the EVA tensionner, can open the compatibility for the upcomming VZ-Bot Al/CF Toolhead set, and the next Flathead V3 iteration. NEED D5M4 Shoulder bolt|[Download](/manuals/Manual-Tensionner-L3VER-M1-A.pdf)|01/06/22| [SHOP](https://store.brs-engineering.com/products/tensionner-l3ver-m1)|[Shop CAD](https://store.brs-engineering.com/products/tendeur-l3ver-m1-a1-1-cad)| 
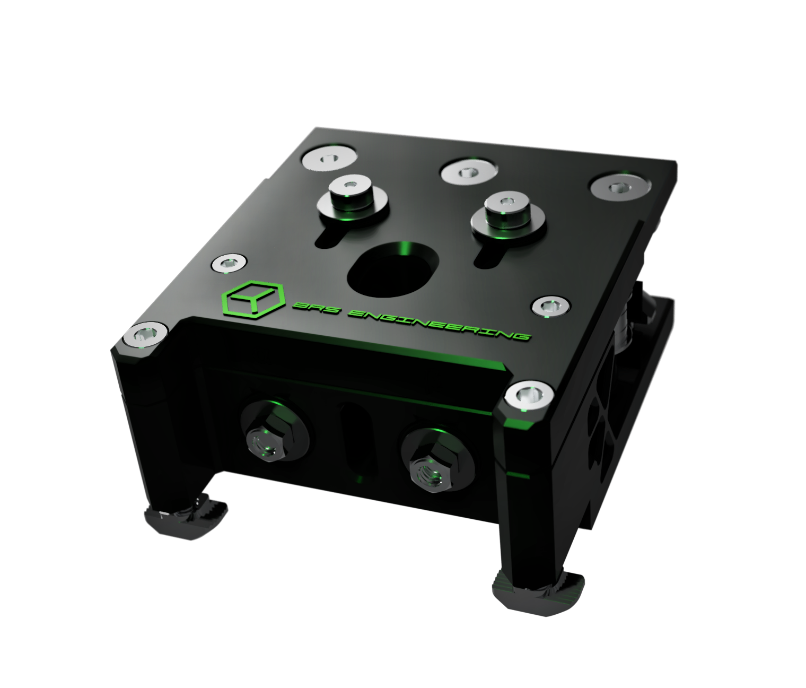
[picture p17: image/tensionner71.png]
L3VER M1 1.1 (A1.6) Tensionner module|Active|<br> **L3VER M1 1.1 A1 Tensionner** A full Vcore 3 compatible manual tensionner block removing the need of the EVA tensionner, can open the compatibility for the upcomming VZ-Bot Al/CF Toolhead set, and the next Flathead V3 iteration. NEED D5M4 Shoulder bolt, This is a revised version from the 1.0, more dense, few parts less, same performances|[Download](/manuals/Manual-Tensionner-L3VER-M1-A.pdf)|01/05/23| [SHOP Soon]()|[Shop CAD Soon]()| 

### PMB Original (Reuploaded)
A full conversion of the stock rear Vcore 3.0/3.1  motor block to secure the shaft with Pulley.
Original mode made in August 2021, deprecated with the L3VER M2 which was the upgrade of it, but still useful with a L3ver M3 setup

Original and AWD version available

Product|Status|View|Manual EN|Release date| Printable |Shop CAD|License
-----------------|------|-----------------------------------| :----: |  :---------------: |  :---------------: |  :---------------: | :---------------:
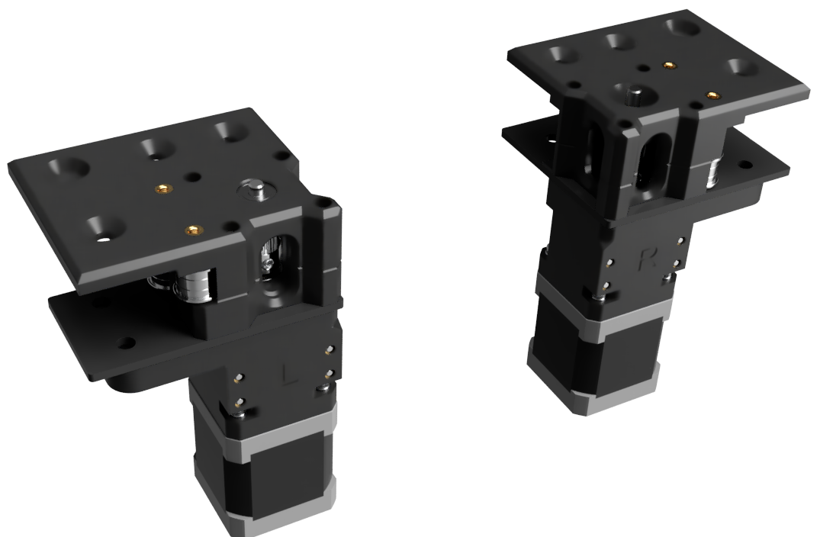
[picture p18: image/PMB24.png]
PMB Original Stock|ACTIVE|<br> **PMB 1.0 Stock** Reinforced rear motor block for a secured nema shaft and a shoulder bolt driven bearings for the best precision and reliability. Works with L3VER M1 (Not compatible with L3ver M2 ||10/08/21|[Files](https://www.printables.com/model/936611-precision-motor-blocks-original-pmb-awd-enclosure)|| 
PMB Original for AWD layout|ACTIVE|**PMB 1.0 AWD** Reinforced rear motor block for a secured nema shaft and a shoulder bolt driven bearings for the best precision and reliability. Works with AWD Drives 1.35, L3VER M3and l3ver M1 (Not compatible with L3ver M2)||08/07/24|| 
PMB Original +AWD layout + Enclosure 2.0|ACTIVE|**PMB 1.0 AWD** Reinforced rear motor block for a secured nema shaft and a shoulder bolt driven bearings for the best precision and reliability. Works with AWD Drives 1.35, L3VER M3and l3ver M1 (Not compatible with L3ver M2)||08/07/24|[Files](https://www.printables.com/model/936611-precision-motor-blocks-original-pmb-awd-enclosure)| 

### L3VER M2
A more drastic integration, lower profile, with an upgraded motor block design to dampen the motor vibrations and noises, and reinforced shaft for more longevity and precision.

-The classic M2 in place of the rear stock block

Product|Status|View|Manual EN|Release date|Shop Product|Shop CAD|License
-----------------|------|-----------------------------------| :----: |  :---------------: |  :---------------: |  :---------------: | :---------------:
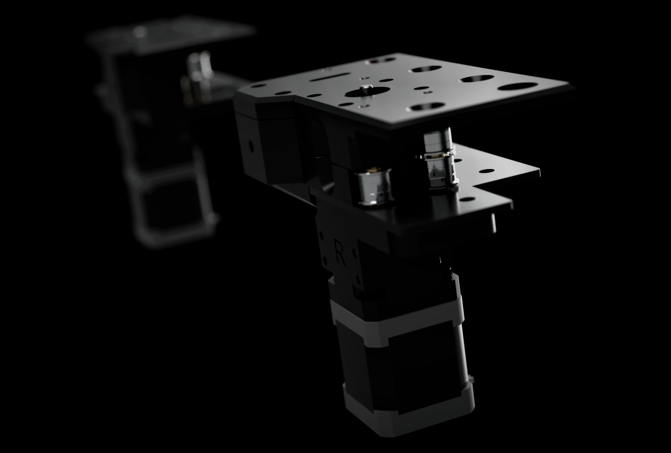
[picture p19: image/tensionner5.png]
L3VER M2 A1 Tensionner module|ACTIVE|<br> **PMB 2.0 L3VER M2 Tensionner** A full Vcore 3 compatible manual tensionner block merged with the PMB mod, removing the need of the EVA tensionner, can open the compatibility for the upcomming VZ-Bot Al/CF Toolhead set, and the next Flathead V3 iteration. NEED D5M4 Shoulder bolt|[Download](/manuals/Lever-m2-manual.pdf)|22/06/22|[SHOP](https://store.brs-engineering.com/products/precision-motor-block-1-0?variant=42850205335801)|[Shop CAD](https://store.brs-engineering.com/products/tendeur-l3ver-m2-a1-0-cad)| 
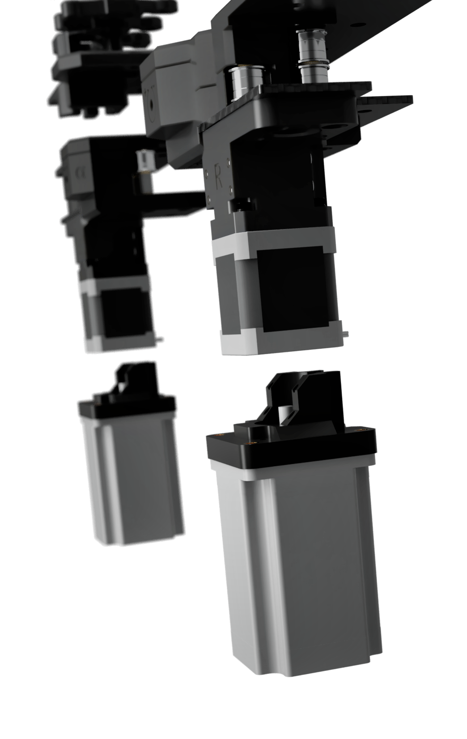
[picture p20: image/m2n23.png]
L3VER M2 A2 Tensionner module|ACTIVE|<br> **PMB 2.0 L3VER M2 Tensionner** First revison,adding the SKL tops, adding NEMA23 compatibility holder (need to swap the electronic bay plate to the front (VC3.x)|[Download](/manuals/Lever-m2-manual.pdf)|21/02/23|[SHOP](https://store.brs-engineering.com/products/precision-motor-block-1-0?variant=42850205335801)|[Shop CAD](https://store.brs-engineering.com/products/tendeur-l3ver-m2-a1-0-cad)| 

### Options for L3VER M1/M2/M3
IF you dont want to change the motor bracket, (very simple installation) Good for already working machines

Product|Status|View|Release date|Shop Product |License
-----------------|------|-----------------------------------| :----: |  :---------------: |  :---------------:
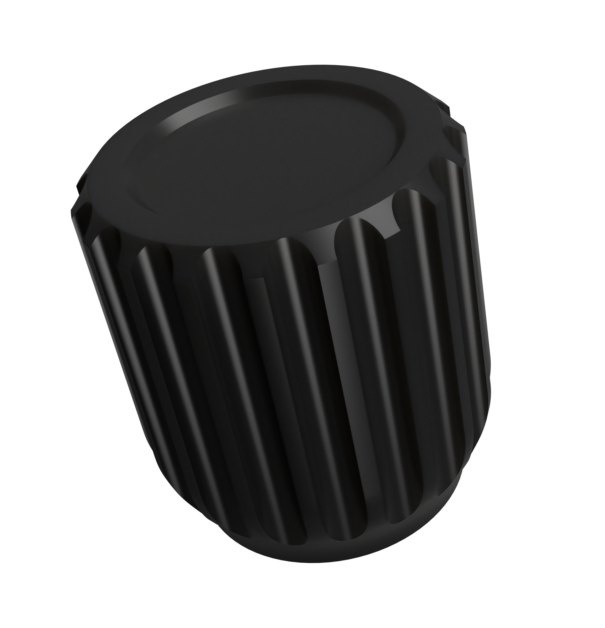
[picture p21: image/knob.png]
M1/M2/M3 Knob |ACTIVE|<br> **Knob M1/M2** A handy knob to adjust the tension without using a tool! Works with all L3VER M1/M2 variations|16/10/2023| FREE on the [STORE](https://store.brs-engineering.com/products/knob-for-lever-m1-and-m2) | NONE

### L3VER M2 TENSIONNER enclosure plates Vcore 3.x (3.0 / 3.1)
Rear part is meant to be printed, the front one is to be cut (metal/PC)

Product|Status|View|Manual EN|Release date|Shop Product| CAD | License
--------|------|---------------------|----|--------------- |--------------|---------------|---------------
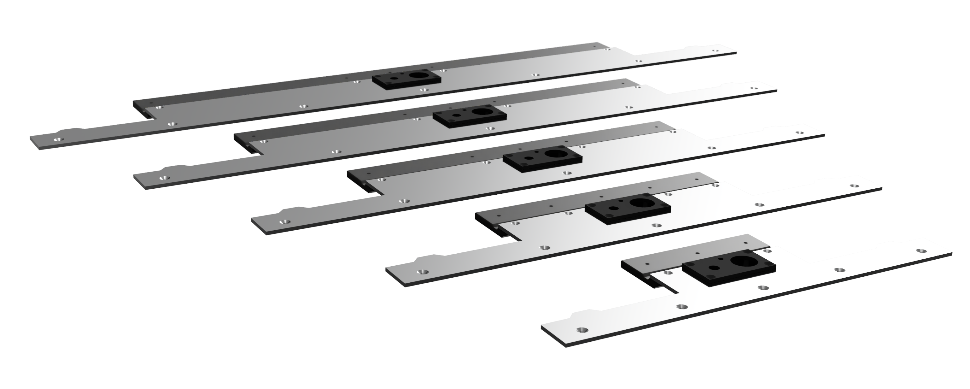
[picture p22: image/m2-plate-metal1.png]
M2 Enclosure plates 1.0|Active|<br> **M2 Enclosure plates** A set of plates to close the rear electronic top for the M2 Lever. Has been designed with the Cpap hole but can be use with any layout you can add; Made for Vcore 3.x 200mm, 300mm, 400mm, 500mm, and 600mm|none|24/05/23|soon|[CAD](/cad/m2-plate.zip)|

### L3VER M2 TENSIONNER WS7040 CPAP enclosure plates Vcore 3.x (3.0 / 3.1)

Product|Status|View|Manual EN|Release date|Shop Product| CAD | Credit
--------|------|---------------------|----|--------------- |--------------|---------------|---------------
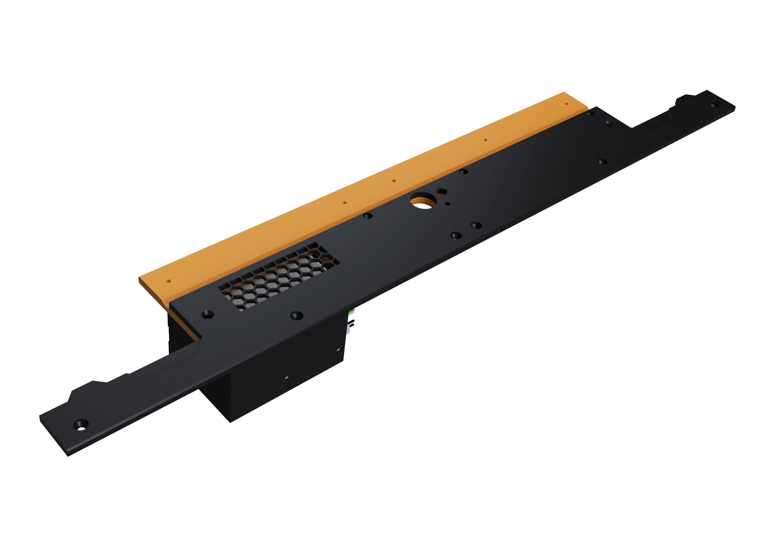
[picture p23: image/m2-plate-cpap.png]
M2/WS7040 CPAP V1.1 - Enclosure plates|ACTIVE|<br> **M2/WS7040 CPAP - Enclosure plates** A set of plates to close the rear electronic top for the M2 Lever. Has been designed with the Cpap hole but can be use with any layout you can add; This iteration use the excellent mod from my friend Dan Cernogorsky, named "RatRig V-Core WS7040 CPAP Fan Shelf Mount", housing the CPAP fan and electronic in a dampered solution meant to reduce the sound of the turbofan, and ease the mounting of it. Made for Vcore 3.x 200mm, 300mm, 400mm, 500mm,|None|24/05/23|[SHOP](https://store.brs-engineering.com/products/l3ver-m2-rear-shelf-with-cpap-silencer-box)|[STEP+STLs](https://www.printables.com/model/867833-brs-shelves-with-cpap-silencer)|[CREDIT](https://www.printables.com/model/354374-ratrig-v-core-ws7040-cpap-fan-shelf-mount/files) | 

### L3VER M1+Refreshed TENSIONNER enclosure plates Vcore 3.x (3.0 / 3.1)
### VC300
Product|Status|View|Manual EN|Release date|Shop Product| CAD | STL | License
--------|------|---------------------|----|--------------- |--------------|---------------|---------------|---------------
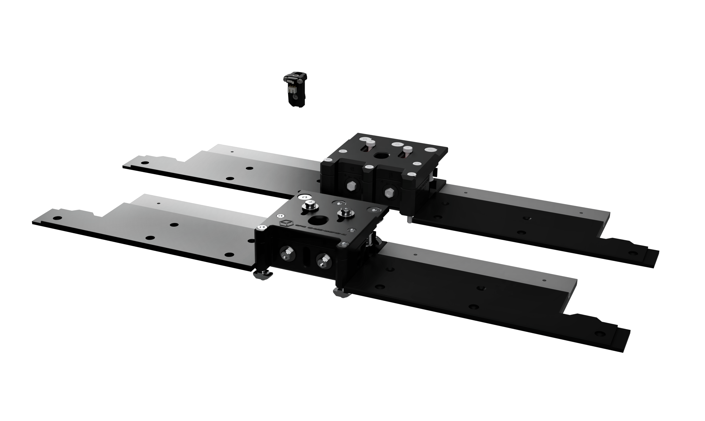
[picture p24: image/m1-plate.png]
M1+refreshed Enclosure plates 1.0|Active|<br> **M1 Enclosure plates** A set of plates to close the rear electronic top for the M1 and M1.1 refresh Lever.|none|soon|soon|[CAD](/cad/m1-300-plate.step)|soon | 
### VC400
Product|Status|View|Manual EN|Release date|Shop Product| CAD | STL | License
--------|------|---------------------|----|--------------- |--------------|---------------|---------------|---------------
M1+refreshed Enclosure plates 1.0|Active|<br> **M1 Enclosure plates** A set of plates to close the rear electronic top for the M1 and M1.1 refresh Lever.|none|soon|soon|[CAD](/cad/m1-400-plate.step)|[STL](https://github.com/FlorentBroise/BRS-Printers-Mod/tree/main/stl/m1-plates) | 
### VC500
Product|Status|View|Manual EN|Release date|Shop Product| CAD | STL | License
--------|------|---------------------|----|--------------- |--------------|---------------|---------------|---------------
M1+refreshed Enclosure plates 1.0|Active|<br> **M1 Enclosure plates** A set of plates to close the rear electronic top for the M1 and M1.1 refresh Lever.|none|soon|soon|[CAD](/cad/m1-500-plate.step)|soon| 

## [Back to Main Page](/README.md)

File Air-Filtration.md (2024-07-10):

## 5/ FILTRATION SOLUTION

- BRS-CF80 Filtration Solution

Keep lungs safe 

Version|Description|ReleaseDate|CAD|Printables|BOM|License|Shop
-------------|-----------|-----------|-----------|-----------|-----------|-----------|-----------
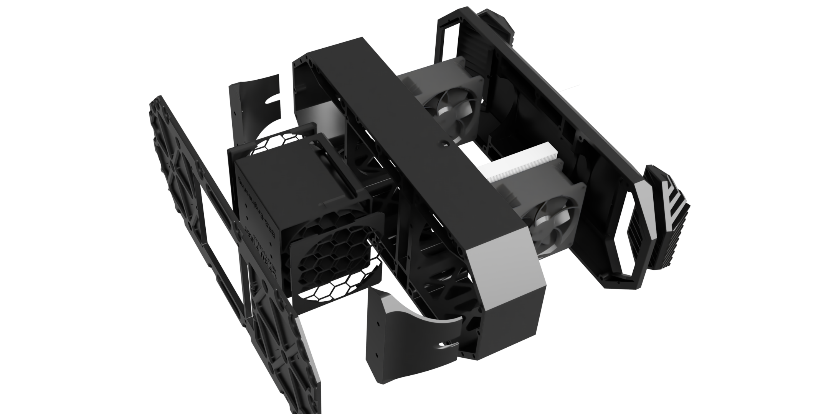
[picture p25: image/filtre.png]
**V1.0**|<br>VCORE 300 / 400 / 500 / +. Heavy duty Filtration system, HEPA + Carbon filter, works on a recirculation principle, perfect for heated chambers |30/01/2022 |[STEP](https://drive.google.com/file/d/1GbbapQNqAy890YhhwPo68B0XPKutEi3w/view?usp=sharing)| [STL](https://www.thingiverse.com/thing:5224729)|/||[STORE](https://store.brs-engineering.com/products/brs-cf80-filtration)
**V1.1**|<br>VCORE 200. Heavy duty Filtration system, HEPA + Carbon filter, works on a recirculation principle, perfect for heated chambers / ITERATION Made by Baptiste FRESSY and Jerôme WIDERMANN [RomRider](https://github.com/RomRider)|28/07/2022 |[STEP](https://github.com/FlorentBroise/BRS-Printers-Mod/raw/main/cad/BRS_Filtre_HEPA-V-Core_200.step)|/|/||[STORE](https://store.brs-engineering.com/products/brs-cf80-filtration)
**V1.2**|<br>VCORE 300 / 400 / 500 / +. Heavy duty Filtration system, HEPA + Carbon filter, works on a Dual Open/closed recirculation principle, perfect for heated chambers or even open frame. A servo contolled flap allow you to chose recirculating or not via Klippe |/ |SOON|SOON|||[STORE](https://store.brs-engineering.com/products/brs-cf80-filtration)
**V1.3**|<br>VCORE 300 / 400 / 500 / +. Heavy duty Filtration system, HEPA + Carbon filter, compatible for the upcoming Open/Close loop switch (Soon available), perfect for heated chambers or even open frame. |10/07/2024|[STEP](https://www.printables.com/model/939151-brs-cf80-heavy-duty-filter))|[STEP](https://www.printables.com/model/939151-brs-cf80-heavy-duty-filter)|[BOM](https://docs.google.com/spreadsheets/d/11ExLfHJaYJ5HMpmTMfWIXNaAl4x_0QrL1ACZfeDynEQ/edit?usp=sharing)||[STORE](https://store.brs-engineering.com/products/brs-cf80-filtration)

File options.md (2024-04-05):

- Heavy spool holder

Version|Description|ReleaseDate|CAD|License|Shop
-------------|-----------|-----------|-----------|-----------|-----------
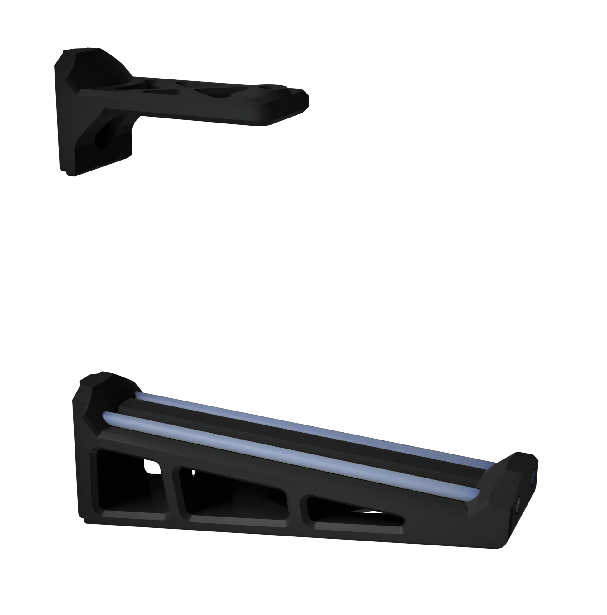
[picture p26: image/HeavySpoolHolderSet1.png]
**V1.0**|<br>A Simple spoolholder with PTFE glider (PTFE tubes), low friction, and 111mm long for large spools. Packed with a PTFE tube guide to adapt the height of the spool for a flawless filament flow |26/05/2023 |[STEP](/cad/Heavy-spool.zip)||[STORE](https://store.brs-engineering.com/products/heavy-spool-holder)

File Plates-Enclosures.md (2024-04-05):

## 4/ PLATES

- Bottom plate DXF

For Z upgrade 2.0 (Not 2.8 DE)

Version|Description|ReleaseDate|CAD|Thingiverse|License
-------------|-----------|-----------|-----------|-----------|-----------
**V2-400**|<br>LEGACY Bottom plate for Z upgrade 2.0 until 2.07|10/01/22|[500](https://github.com/FlorentBroise/BRS-Printers-Mod/raw/main/cad/Panel_base_BRS-500.dxf) [400](https://github.com/FlorentBroise/BRS-Printers-Mod/raw/main/cad/panel_base_BRS-400.dxf) [300](https://github.com/FlorentBroise/BRS-Printers-Mod/raw/main/cad/panel_base_BRS-300.dxf)

- Lid Backplate 

For BRS-CF80

Version|Description|ReleaseDate|CAD|Thingiverse|License
-------------|-----------|-----------|-----------|-----------|-----------
**V1-400**|<br> for BRS-CF80|06/03/22|[500 with corner](https://github.com/FlorentBroise/BRS-Printers-Mod/raw/main/cad/Backplat500stock.dxf) [400 cornerless](https://github.com/FlorentBroise/BRS-Printers-Mod/raw/main/cad/Backplate.dxf) [300](to do)

## 6/ Spool Holder

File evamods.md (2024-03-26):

# EVA 3.x Mods

## 1. Tensionnerless EVA 3.x Back

Version|Description|ReleaseDate|CAD|Store
-------------|-----------|-----------|-----------|-----------
**V1.0**|EVA 3 Back without tensionner, to use with the L3VER M2 / M1 system|04/04/23|
**V1.1**|<br> Minor fix to reduce the screw lenght by adding more deeper hex/Fi holes|31/08/23|[STEP / STL Package](https://github.com/FlorentBroise/BRS-Printers-Mod/tree/main/cad/EVA-Back-1.zip) |[STORE](https://store.brs-engineering.com/products/eva-3-x-tensonnerless-for-l3ver-m1-m2)

# RatRig Toolhead 2023 Mods

## 1. Tensionnerless RatRig ToolHead Back

Version|Description|ReleaseDate|CAD|Store
-------------|-----------|-----------|-----------|-----------
**V1.0**|Ratrig Toolhead Back without tensionner, to use with the L3VER M2 / M1 system|31/10/23|
**Beta1.0** DEPRECATED |<br> Ratrig Toolhead Back without tensionner, to use with the L3VER M2 / M1 system / Reinforced upper belt section!!!! This toolhead proved to be basically bad design especially on the Belt grabber section which suffer fatigue ove time, BETA 2 is advised but doesnt support a full tensionner delete. It can be used anyway with L3VER products|31/10/23|[STEP / STL Package](https://github.com/FlorentBroise/BRS-Printers-Mod/tree/main/cad/RRT-Back-1.zip) |[STORE](https://store.brs-engineering.com/products/ratrig-tool-head-printed-parts-only?variant=47264346800475)
**Beta2.0**|Ratrig Toolhead Back with tensionner, to use with the L3VER M2 / M1 system. The Beta 1 toolhead proved to be basically bad design especially on the Belt grabber section which suffer fatigue ove time, BETA 2 is advised but doesnt support a full tensionner delete. It can be used anyway with L3VER products|26/03/24|

# EVA 2.4.x Mods

## 1. Light ADXL Shroud

Version|Description|ReleaseDate|CAD|
-------------|-----------|-----------|-----------
**V1.0**|ADXL345 holder with light specs|23/07/21|[STL](https://github.com/FlorentBroise/BRS-Printers-Mod/tree/main/cad/shroudbrs.stl)
**V1.0**|Duct made for a Volcano heatblock to Hemera system|23/07/21|[STL](https://github.com/FlorentBroise/BRS-Printers-Mod/tree/main/cad/Duct_volcano.3mf)

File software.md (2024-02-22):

##CURA 4.13.0 Tips

### RomRider Fast Gyroid Infill  
A script tweak allowing to drastically reduce infill time for Gyroid

https://github.com/RomRider/klipper-FastGyroidInfill

### BRS Cura Profile
Here some free profiles, Speeds here are not a the max capacity of the machine, you can tune it a bit, made on purpose to reach high quality and below +-0.03mm of variance on XYZ for professionnal activity. Made for the BRS-E Vcore3 edition with the Flathead V2 profile

Material|Objective|Filament Brand|cura-profile
-----------------|------|-----------------------------------| :---------------:
ABS/ASA | Hight quality/High accuracy| EmotionTech/3DJake| [Download](/cura/BRS-E-ABS-ASA.curaprofile)
PLA | Hight quality/High accuracy| EmotionTech/3DJake/EcoFil/Polyterra| [Download](/cura/BRS-E-PLA.curaprofile)

### CURA Material cost and power cost

You need to make a material profile, fill the density, net weight of the spool, and the price you've paid for it



Then for the power cost, you need a Plugin name "Power Cost"



Under Machine settings, there is now a power cost tab, implement the price per KWh and the average power drow of the machine (once printing is started, after the bed and heater at temperature)



Now once the Slicing is made, you can see the costs for the part



### Flow Fine tunning

As Flow is the most important factor regarding to quality, bonding, and dimentionnal accuracy; I strongly advise to enable all factors in the settings.
This will allow you to achive perfect print on all aspect



Remember that external wall flow can impact the dimentionnal accuracy. 
I'm personnally making the flow tuning before the rotation_distance tunning. This way I'm actually able to achieve 0.05-0.08mm precisions
I advise to make the rotation_distances tuning once a week, just measure the part, compare it to what was expected, and use the [conversion tool](https://docs.google.com/spreadsheets/d/12R55MfSqfu5xPplTaRvmbkXf2mHBpJ3Zlwajab_pi60/edit?usp=sharing) to fine tune overtime. This will make better part over the time, and maintain the dimentionnal accuracy accurate relative to Belt shrinkage over time, temperature variation, "wear" of the machine

## [Back to Main Page](/README.md)

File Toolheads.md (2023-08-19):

## 3/ TOOLHEAD

- EVA 3.x Magnum+ / VZ Extruder
v-1.0
A light Mosquito Magnum+ based toolhead, with the VZbot ultra light extruder

Version|Description|Details|CAD|Release date|License|Order
-------------|-----------|-----------|-----------|------------|------------|-----------
**V1.0-VZ-MosquitoM+**|| | [STEP](/cad/Flatheadv2.zip)|16/01/23||[SHOP](https://store.brs-engineering.com/products/eva-3-x-cartesian-inserts-magnum-plus-vz-extruder2)
**V1.0-M+ Duct Corrected**|| | [3MF](/cad/MplusDuct.3mf) |25/01/23||[SHOP](https://store.brs-engineering.com/products/eva-3-x-cartesian-inserts-magnum-plus-vz-extruder2)

- FLATHEAD V2
v-b0.2 
A ultralight mosquito based toolhead, with Crystal geometric shroud face

Version|Description|Details|CAD|Release date|License|Order
-------------|-----------|-----------|-----------|------------|------------|-----------
**V1.20-LGX-Lite Mosquito**|| LGX-Lite, berd-air, Mosquito, Carbon fiber PA6CF and titanium based head, compatible Mellow Mini AB, direct wiring, Huvud 0.61, FLY-SHT-42|  [Files](/cad/Flatheadv2.zip) [Shroud](/cad/Shroud.zip)|17/03/22||[SHOP](https://www.brs-engineering.com/Flathead-Toolhead.html)
**U1.0a-Cooling upgrade**|| High flow focused pipes to unlock high speed PLA, better overall flux dynamics|SOON|05/05/22|
**V1.21b-LGX-Lite Mosquito**|| Mellow FLY-SHT-36 Adaptation|  [STEP](/cad/sth36.zip)|27/03/22|
**V1.22a-LGX-Lite Mosquito**|| BL-Touch adaptation / Inductive 8mm|  [STEP](/cad/BLIND.zip)|02/04/22|
**V1.22b-LGX-Lite Dragon Liquid/NFC**|| Dragon Liquid/BMO/NF crazy plate(beta) and shroud. The plate can be CNC or PA6C20 type 100% infill material|  [STEP](/cad/dragon.zip)|06/04/22|
**V1.22c-LGX-Lite Dragon**|| Dragon plate(beta) and shroud. The plate can be CNC or PA6C20 type 100% infill material|  [STEP](/cad/dragon.zip)|/|
**V1.22d-LGX-Lite Nova**|| Nova plate(beta) and shroud. The plate can be CNC or PA6C20 type 100% infill material|  [STEP](/cad/nova.zip)|/|
**V1.23a-LGX-Lite Mosquito**|| ERCF compliant|  [Files (soon)]()|/|

- FLATHEAD V3

A ultralight mosquito based toolhead, "tensionnerless" with a Crystal geometric shroud face and the CANBus new iteration

Version|Description|Details|CAD|Release date|License|Order
-------------|-----------|-----------|-----------|------------|------------|-----------
**V1.0-LGX-Lite Mosquito**|| LGX-Lite, quad pipes berd-air, Mosquito, Carbon fiber PA6CF and titanium based head, compatible Huvud 0.61, BTT CAnbus squared board and Mellow CANbus Squared board|/|07/22|CC-BY-NC-ND-4.0|

- BRS-HextrudORT

HEVORTs toolhead adaptation

Version|Description|Details|CAD|ReleaseDate|License
-------------|-----------|-----------|-----------|------------|------------
**V0.2-BRS-HextrudORT BETA**|| Naked of Probe version. Based on the MirageC wonderful design from the [Hevort project](https://miragec79.github.io/HevORT/). Displayed her with the Nova, can be equiped with every hotend variation from the [Hevort Page](https://miragec79.github.io/HevORT/), be careful to the Z probe Height, compatible with the new Gantry V2 | [Files](/cad/toolheadv2.step)|18/03/22|
**V0.21-BRS-HextrudORT BETA**|| Euclid Probe version, can be equiped with every hotend variation from the [Hevort Page](https://miragec79.github.io/HevORT/), be careful to the Z probe Height, compatible with the new Gantry V2 | [Files](/cad/toolheadv3.step)|22/03/22|

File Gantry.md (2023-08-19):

## 2/ XY MOTION

- UltraLight Gantry XY 

Version|Description|ReleaseDate|CAD|Files|License|ShOP
-------------|-----------|-----------|-----------|------------|-----------|-----------
**vb3.1**(ACTIVE)| Belt tension center corrected, 290g removed from the previous system AVAILABLE for Print service at BRS-E <br> |10/03/2022|[STEP](https://drive.google.com/file/d/1E_F52YKvfQOkNzmlE50xRKSoCSYZyfMS/view?usp=sharing) [FILES](https://github.com/FlorentBroise/BRS-Printers-Mod/raw/main/cad/CFGantryV2.zip)||
**vb3.2**(ACTIVE)| UNDER Rail - Iteration to adapt natively on stock Ratrig plates, or CF version from 3rd party vendors AVAILABLE for Print service at BRS-E (Prefer a Z1 preload MGN9H)<br> |10/03/2022|[STEP](https://github.com/FlorentBroise/BRS-Printers-Mod/raw/main/cad/GantryV2b.step)|||[SHOP](https://www.brs-engineering.com/Flathead-Toolhead.html)
**vb3.2.1-FIX**(ACTIVE)| FIX of the 20x20 hole dimensions to be more tight over the tube<br> |26/06/2022|[STEP/STL](https://github.com/FlorentBroise/BRS-Printers-Mod/raw/main/cad/Ultralight-Joiner-CF-Adjusted1.zip)|||[SHOP](https://www.brs-engineering.com/Flathead-Toolhead.html)
**vb3.3**(ACTIVE)| TOP Rail ( EVA ) - Iteration to adapt natively on stock Ratrig VC3.0 plates, or CF version from 3rd party vendors AVAILABLE for Print service at BRS-E (Prefer a Z1 preload MGN9H)<br> |26/06/2022|[STEP/STL](https://github.com/FlorentBroise/BRS-Printers-Mod/raw/main/cad/Ultralight-Joiner-CF-Adjusted.zip)|||[SHOP](https://www.brs-engineering.com/Flathead-Toolhead.html)
**vb3.4**(DEPRECATED)|  TOP Rail ( VZ bot ) - SHOULDER BOLT/M5 - Iteration to maximize X dimension for the VZbot Printhead, (Prefer a Z1 preload MGN9H ONLY)<br> |27/06/2022|[STL](https://github.com/FlorentBroise/BRS-Printers-Mod/raw/main/cad/Ultralight-Joiner-CF-Adjusted2.zip) / [STEP](https://github.com/FlorentBroise/BRS-Printers-Mod/raw/main/cad/Ultralight-Joiner-CF-Adjusted3.zip)|||
**vb3.5a**(Active)|  TOP Rail ( VZ bot ) - SHOULDER BOLT - Iteration to maximize X dimension for the VZbot Printhead,  !!FOR VC3.1<br> |12/09/2022|[STEP](https://github.com/FlorentBroise/BRS-Printers-Mod/raw/main/cad/VC31SBstd.zip)|||Print Service[SHOP](https://store.brs-engineering.com/products/vcore-joiners-for-vz-toolhead)
**vb3.5b**(Active)|  TOP Rail ( VZ bot ) - M5 - Iteration to maximize X dimension for the VZbot Printhead, M5 Stock fixation, !! FOR VC3.1<br> |12/09/2022|[STEP](https://github.com/FlorentBroise/BRS-Printers-Mod/raw/main/cad/VC31std.zip)|||Print Service[SHOP](https://store.brs-engineering.com/products/vcore-joiners-for-vz-toolhead)
**vb3.5c**(Active)|  TOP Rail ( VZ bot ) - SHOULDER BOLT - Iteration to maximize X dimension for the VZbot Printhead, More stable Join than 3.4 version, ready for Optical X endstop. Low weight (20g/each with PA12CF15) (Prefer a Z1 preload MGN9H) !! FOR VC3.0 and BRS-VULCAIN<br> |12/09/2022|[STEP](https://github.com/FlorentBroise/BRS-Printers-Mod/raw/main/cad/VC30VULC.zip)|||[SHOP](https://store.brs-engineering.com/products/vcore-joiners-for-vz-toolhead)

- Euclid Probe parts 

Version|Description|ReleaseDate|CAD|Files|License
-------------|-----------|-----------|-----------|------------|-----------
**EPD1.1**(ACTIVE)| Euclid Dock probe fot the Flathead/BRS-HextrudORT (Vcore3) AVAILABLE for Print service at BRS-E <br> |19/03/2022|[STEP](https://github.com/FlorentBroise/BRS-Printers-Mod/raw/main/cad/EPD.step) ||

- Precision modular Motors blocks

Version|Description|ReleaseDate|CAD|BOM|License|Order
-------------|-----------|-----------|-----------|-----------|-----------|-----------
**PMB1.1**|<br> Replacement parst to add Shoulder bolts in place of the standard m5 bold for better precision in the motion system, in the same time it help to reduce vibrations and noises because dampening effect of the printed part and the coupling. Needs 625ZZ bearings, 5mm shafts|21/03/2022 |[Files](https://drive.google.com/file/d/1kFUzjTdgDCWAe0plJPDxEhb_yOU4WQ-o/view?usp=sharing) [STEP](/cad/PMB1.zip)|[BOM](/bom/BOM_PMH.xlsx)||[SHOP](https://www.brs-engineering.com/Heavy-duty-motor-block.html)
**Dampers option**|<br> add a Nema damper to reduce noises and improve responsivness (tested)|24/03/2022 ||[Info](https://www.moonsindustries.com/series/dampers-a020202)|
**PMB1.2**|<br> Iteration compatible with extended Z extrusion for integrated enclosure mods and open front mod|02/04/2022 |[STEP](/cad/PMB12.zip)|[BOM](/bom/BOM_PMH.xlsx)||[SHOP](https://www.brs-engineering.com/Heavy-duty-motor-block.html)
**PMB1.3**|Compatibility with larger Disc coupling options, up to L28xD30mm|15/05/2022 |/|/||[SHOP](https://www.brs-engineering.com/Heavy-duty-motor-block.html)
**PMB2.0a**|<br> PMB with L3VER tensionner incorporate, for stock Vcore3 (Open VZbot toolhead design)|10/06/2022 |[CAD is available on the STORE](https://store.brs-engineering.com/products/tendeur-l3ver-m2-a1-0-cad)|[BOM](https://github.com/FlorentBroise/BRS-Printers-Mod/blob/main/bom/BOM-M1-M2.pdf)||[SHOP](https://www.brs-engineering.com/Heavy-duty-motor-block.html)
**PMB2.0b**|PMB with L3VER tensionner incorporate, for open front mod (Open to VZbot toolhead design)|10/06/2022 |[CAD is available on the STORE](https://store.brs-engineering.com/products/tendeur-l3ver-m2-a1-0-cad)|[BOM](https://github.com/FlorentBroise/BRS-Printers-Mod/blob/main/bom/BOM-M1-M2.pdf)||[SHOP](https://www.brs-engineering.com/Heavy-duty-motor-block.html)
**SKL-1.0**|<br>Top plate for the L3VER M2 tensionner. Generated with topology study, allow a very light part, and an original open heart skeleton design.|07/09/2022 |[STEP](/cad/SKL-1-M2.zip)|[BOM](https://github.com/FlorentBroise/BRS-Printers-Mod/blob/main/bom/BOM-M1-M2.pdf)||[SHOP](https://florent-broise.myshopify.com/products/l3ver-m2-skeleton-top)

- BRS-Open Front Mod

Version|Description|ReleaseDate|CAD|BOM|License|Order
-------------|-----------|-----------|-----------|-----------|-----------|-----------
**BOF-V1**|<br> Replace the stock idler, allow to remove the front 3030 extrusion to clear the view. Intended to be use with the Z-Ugrade (all versions), with EVA tensionner system OR with the upcoming L3VER M tensionner for the VC3; Needs 6x M6x20 and 2 5x55m steel shafts |19/05/2022 |[R](/cad/stl/OFR.stl) [L](/cad/stl/OFL.stl) | || [SHOP](https://florent-broise.myshopify.com/products/open-front-idlers)
**BOF-V1**|<br> Replace the stock idler, allow to remove the front 3030 extrusion to clear the view. Intended to be use with the 3.1/3.1/Ventermech versions, with EVA tensionner system OR with the upcoming L3VER M tensionner for the VC3; Needs 6x M6x20 and 2 5x55m steel shafts |07/11/2022 |[U](/cad/xy_idler_v1.2_W.step) | || [SHOP](https://florent-broise.myshopify.com/products/open-front-idlers)
**BOF-Modular-V2**|<br> Replace the stock idler, allow to remove the front 3030 extrusion to clear the view. Intended to be use with the Z-Ugrade (all versions), with EVA tensionner system OR with the L3VER M Series tensionner for the VC3. Made for the VC3.0/3.1, compatible with the 2.0 Enclosure, and have the flexibility to be used with: the stock 3.1 leadscrews jigs, the Z-Upgrade 1.6-1.99 SFU retainers , and the upcoming VULCAIN variation |20/10/2022 |[Universal STEP (mirror it)](/cad/BOF2.step)| || [SHOP](https://florent-broise.myshopify.com/products/brs-open-front-idlers-v2-0)

- Stock Enclosure simplification Jigs

Version|Description|ReleaseDate|CAD|License
-------------|-----------|-----------|-----------|-----------
**V1.0**|<br> in order to remove the front 2x 3030 to enlighten a bit the design from the front view|18/04/22|[part-3MF](https://github.com/FlorentBroise/BRS-Printers-Mod/raw/main/cad/Enclosure_bracket.3mf)|

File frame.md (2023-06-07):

# Upgrades

#The shop has moved to https://store.brs-engineering.com/

BRS-Vulcain I Frame

Version|Description|ReleaseDate|BOM|CAD|Documentation|License|Order
-------------|-----------|-----------|-----------|------------|------------|-----------|-----------
**V1.0**|<br> A blind Join Assembled Frame, Can be adapted to a VC3.0-3.1 or adapted for the Vulcain Design.|01/09/22|[Files](https://github.com/FlorentBroise/BRS-Printers-Mod/tree/main/image/framesize.png)|[STEP](https://github.com/FlorentBroise/BRS-Printers-Mod/blob/main/cad/Vulcain-Frame-Assembly.step)||

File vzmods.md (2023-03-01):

# VZ Mods

## 1. VZ toolhead + extruder , CAN adapter (SHT36v2)

Version|Description|ReleaseDate|CAD|SHOP
-------------|-----------|-----------|-----------|-----------
**V1.0**|<br> Strong structure to hold SHT style CAN bus boards, for VZ toolhead and VZ Extruder|01/03/23|[STEP](https://github.com/FlorentBroise/BRS-Printers-Mod/tree/main/cad/Vz-PrintHead-VZextruder-CANHolder.zip) | [STORE](https://store.brs-engineering.com/products/can-bus-board-holder-for-vz-toolhead)

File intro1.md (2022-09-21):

# The VULCAIN 



Vulcan is an ancient Roman god, whose parents are Juno and Jupiter.
God of iron and fire, and therefore of blacksmiths, the hammer is his attribute. He was identified with the Greek god Hephaestus.
As a Mythology lover, this name is self explainable

This Machine is a mix of every mod/upgrade I developped/worked on, and found relevent to make a Industrial effective machine, 
with the best longevity, repetability and low maintenance, with a lot a glam of course time
It has been developped in mind to be scaled safely to 1200mm^3, maybe more

Partially based on the Vcore COREXY system, The new Z system is made upon the Hevorts kinematic bases, with an overall huge rework. 
All BRS previous parts concerning the PMB, L3VER are compatible with it. 
A standard VCore can be used to buil it, but will require few modification concerting the Frame, in other things

The machine is actually sitting in my workshop, waiting to make the very first move.
What is actually done:

-Vzbot toolhead integration with Takoto HE20 Hotend
-Piezo integration in the Vz toolhead (the bigest challenge)
-Z kinematic is finished and fonctionnal

Once the Machine will be validated, something you can follow on the BRS Facebook page, I will realease the CAD, for free, and add kits in the BRS STORE!!
This should happen until the end of September 22! All VULCAIN parts and design are under CC BY-NC 4.0

I see you there :)

# Licence?

Those upgrades are for most of them part of the Creative commons CC BY-NC 4.0, All rights are exclusive to Florent BROISE / BRS-TECH.
Modifications are possible but don't forget this was designed this way for reasons, I'm not responsible of a bad redesign by others. If modifications are needed, you can submit it to contact@brs-engineering.com
For a request concerning a particular case for commercial use, only Florent BROISE / BRS-TECH can agree to a derogation. Feel free to ask :)

[Back to Main Page](/readme.md)

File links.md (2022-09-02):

# Products and usefull things links 

No|Product|Objective|Links
-----------------|------|-----------------------------------| :---------------:
1| EKWB D5 Holder| Trianglelabs style diaphragm pump decoupler/holder|https://www.ekwb.com/shop/ek-revo-d5-pump-mount

# Store Checklist

No|Product|Objective|Links
-----------------|------|-----------------------------------| :---------------:
1| VC3 Checklist|Check after reception| https://www.brs-engineering.com/files/Checklist.pdf

## [Back to Main Page](/README.md)

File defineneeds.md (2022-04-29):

# Defining the needs for your printer

You have to sort out what are your real needs.
Upgrade can satisfy a specific fonction or need but always get a drawback, most of the time.

Example!

# Z-Original vs Z-Ballscrew upgrades?
### PRO's
- Reliable.
- More accurate
- Support heavier charges
- Low maintenance
- No wearing (longer lifspawn and potential downtime)

### CON's
- Not always cheap ? (8% average of the full machine price)
- Z loss of +/-30mm
- Noisier?

# Oldham vs Wings?
### PRO's
- Reliable.
- More accurate
- No rotationnal Backlash compared to wings

### CON's
- PACF to print?
- Z loss of +/-45mm

# Ultraslight Gantryv vs Stock gantry?
Intended Ultralight with F695 and shoulder bolts
### PRO's
- Lighter
- More accurate
- Less noise
- No bearing failures compared to the strandard RR or Mellow Pulleys

### CON's
- Dealing with CF materials?

# Flathead V2 vs EVA?

### PRO's
- Lighter
- Less parts (2 vs 6+)
- No overhanging masses
- Low center of gravity, aligned and balance between rails
- Less vibration (better input shaper values)
- Maintenance easy
- Modifications without detensionning the belts
- HUVUD 0.61, CANbus and MinaAB compatible
- Cable management
- Euclid probe ultra-dense integration

### CON's
- Berd Air?
- Euclid probe?

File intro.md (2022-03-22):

# Upgrades?  
The Vcore3 offer a strong base to modify for eiter specific needs or better prints
You will find here parts and design I think are relevant
The Z upgrade is the first of the upgrade to be available
Will follow a lot more...

As always i have a company, BRS-Engineering, which propose a print service for industrial grade materials if needed

https://www.brs-engineering.com/

# Licence?

Those upgrades are for most of them part of the Creative commons CC BY-NC 4.0, All rights are exclusive to Florent BROISE / BRS-TECH.
Modifications are possible but don't forget this was designed this way for reasons, I'm not responsible of a bad redesign by others. If modifications are needed, you can submit it to contact@brs-engineering.com
For a request concerning a particular case for commercial use, only Florent BROISE / BRS-TECH can agree to a derogation. Feel free to ask :)

[Back to Main Page](/readme.md)

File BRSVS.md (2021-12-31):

Here the BRSVS Air module.



WHAT-WHY-HOW:

0/ BRSVS?
This is a dual auxiliary fan cooling part system, deported from the head to the sides, to loose weight, and bring tons of CFM.

1/ The objective
Bring a high volume of laminar flux of air to the nozzle space to be able to reach high speed motions for PLA, in other things, and remove the fan cooling system from the head.
(It can be used with both)

 -The mod is made by 2 parts:
 1-the base part (fixed), housing fans and the first channel stage duct.
 2-the hose part, which can be modded to achieve different compression, angles, and output designs.
 
2/ Mounting points
 The base part can be mounted in 2 ways:
 -1 On the side pannel (tpu join seal for dampening vibration advertised)
 -2 on a 30x30 vertical extrusion 
 
3/ Hose part
The hose parts in the pack is adapted to a standard Vcore laterial clearance for movement and Z-Tilt
But it can be modified to fit larger models, or a different channeling design

3/ Fans:
Fans needed are quite easy to source, it hase be based on the San-Ace Denky 40m counter ratating module. Those are Server fan for 1u server most of the time.
I chose them because the use to fit the lateral space on the Vcore, and are able to a very high output at a very high static pressure.
At 100% they are very noisy but in my tests, a 30% value still send a enormous amount of air volume at a very acceptable noise. Closing the printer can helps too.

WARNING: Each fan is made by two fans, counter rotating, you will need to rewire them in order to simplify them

4/Power
Those 8 fans (16) draw 12w at 100% each. That mean you have to power it correctly. 
CHECK YOUR PSU CAPACITY TO HANDLE IT

They are 12V, which mean you need to get a 12V auxiliary PSU(100W mini) or a more classical 24v 360W PSU paired with a 24-12v 10-20A step down module (https://www.amazon.fr/gp/product/B07ZV76NLC/ref=ppx_yo_dt_b_asin_title_o05_s00?ie=UTF8&psc=1).
The control of those fan is made by a MOSFET (https://www.amazon.fr/gp/product/B074L1CMYB/ref=ppx_yo_dt_b_asin_title_o04_s00?ie=UTF8&psc=1), directly linked to a GPIO of you Pi

[Wirings(simplified)](https://github.com/FlorentBroise/RatRig-Upgrades/raw/main/image/BRSVSwirings.png)

[STEP SOON](https://github.com/FlorentBroise/RatRig-Upgrades/raw/main/cad/BRSVS1_2b.zip)

DISCLAIMER: The mod in under pre-release state, some tiny changes could occur.

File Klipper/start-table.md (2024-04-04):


Chapter|Content Description
:---: |-------------------
1.|[Disclaimer](/Klipper/Klipper-disclaimer.md)
2.|[Install](/Klipper/Installation.md)
3.|[Printer.cfg](/Klipper/printer-cfg.md)
4.|[Shaper](/Klipper/shaper.md)

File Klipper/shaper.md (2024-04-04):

# INPUT SHAPER

Make sure your ADXL based module is configured correctly
The way this one is attached to the toolhead will matter a lot, a loosy fixation a placment will result a bad shaping
The best place is in the nozzle (the BTT ADXL V2 is the best option IMO). You will use it only on this occasion and then removed it after use

Keep in mind that getting a not perfect shaper is not the end of the world, it is here to counterbalance thos issues.
Only the print result count at the end of the day

First check the acceleromete fonction nwith ```ACCELEROMETER_QUERY``` in the printer CLI
you should get something like this
```
Recv: // adxl345 values (x, y, z): 470.719200, 941.438400, 9728.196800
```
Then run 
```
TEST_RESONANCES AXIS=X
```
```
TEST_RESONANCES AXIS=Y
```

and finally those lines in the  Putty instance
```
~/klipper/scripts/calibrate_shaper.py /tmp/resonances_x_*.csv -o /tmp/shaper_calibrate_x.png
```
```
~/klipper/scripts/calibrate_shaper.py /tmp/resonances_y_*.csv -o /tmp/shaper_calibrate_y.png
```

you can now grab the PNGs of the shaper and make you analysis

# BELT TENSION RESONNANCE
```
TEST_RESONANCES AXIS=1,1 OUTPUT=raw_data
```
```
TEST_RESONANCES AXIS=1,-1 OUTPUT=raw_data
```

Then run this line in PUTTY the instance:
```
~/klipper/scripts/graph_accelerometer.py -c /tmp/raw_data_axis*.csv -o /tmp/resonances.png
```

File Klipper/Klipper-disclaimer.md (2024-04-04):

# Disclaimer:
This page is still under construction, I'm implementing content I will found legit to make a Pure straightforward Klipper/Mainsail setup, this is exactly the way I'm making my machines. It is not a complete guide, it is here to guide you for the main setup. You must build the printer cfg according the pinout layout and your specific hardware. you must be sure that the cables are correctly set to be fonctionnal too, this guid is not a wiring guide.

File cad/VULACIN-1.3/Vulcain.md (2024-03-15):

# VULCAIN V1.3

#The shop has moved to https://store.brs-engineering.com/

BRS-Vulcain 

Version|Description|ReleaseDate|BOM|CAD|Documentation|License|Order
-------------|-----------|-----------|-----------|------------|------------|-----------|-----------
**V1.3**|<br> Actual design of the last VULCAIN iteration, equip the BRS Wworkshop and some machines made for specific customers. Featured All VCORE Upgrades, LEVER M2 are not included in the CAD since it is a paid design, I can send the Full cad on request if CAD M2 have been bought|15/03/23|/|[STEP/F3Z](https://drive.google.com/file/d/173EmpmfSHBIcyloCmVUZlkv9UNQJufjT/view?usp=sharing)|/| | contact@brs-engineering.com [FULL CAD](https://store.brs-engineering.com/products/vulcain-printer-v1-3-cad)

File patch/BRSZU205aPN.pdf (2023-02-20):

# BRS-Engineering


20/02/2023 - Z-Upgrade 2.05a PATCH NOTE

1-[FIX] Holes resize from 5mm to 6.4mm for Ruthex heat inserts :

2-[FIX] Rear NEMA17 holes refited to adapt a m3x35 instead of a short lenght m3x30 :

3- [ADD] New front arms designed to adapt the 3.1 rails layout, opening compatibility to RR Stock 2.0 Enclosure

4- [ADD] Those new arms featured a shorter thickness to gain 5mm more over Z distances, and has a different structure to be more rigid due to the less stable fonction over the 3.0 layout (IMO)


5-[FIX] -3mm holes recess to have more of the screw inside the T nut on the back retainer with m6x14 (stock RR)

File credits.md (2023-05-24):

# Credits: 
Here few people/Companies who I want to thank, for inspiring reasons, constructive discussions, engineering skills, work and vision in general. Consider looking in their work, and donate to support their constant effort by pushing 3D printing forward:

-Olivier Royer-Tardif / MirageC [Hevort project](https://miragec79.github.io/HevORT/)

      A true visionnary by opening the 3D printer worlds to new horizons IMHO

-Simon Vez [VzBot](https://github.com/VzBoT3D/VzBoT-Vz330)

      Putting the VZBOT project on feet and working so hard to bring us more new ways of increasing quality and speed, and a friend!

-Jerôme Wiedemann [RomRider](https://github.com/RomRider)

      He gave me the occasion to speed up my production time, with his Infill speed mod!

-Pawel Kucmus [EVA](https://main.eva-3d.page/)

      Pawel designed a whole ecosystem that is very relevant for a lot of us
      
-Keegan Wentz (Wentz-dynamics)

      Some serious discussion were made about hardcore upgrades ;)
      
-John Beima

      Even with our last disagreaments, John was there back in the time to bring some interesting stuff in the front of the scene

-Oleg Ok [EvoMotors](https://www.thingiverse.com/evomotors/designs) 

     Adapted the ring Wobble design to a new level !

-RatRig Team [Page](https://ratrig.com/v-core3default.html)

     Thanks to the RR team for letting me using their designs to work with ;)

-Fabreeko / Honey Badger [Page](https://www.fabreeko.com/collections/fabreeko)

    A friend and a serious dude when it come to propose quality services
    
-Max Mueller / SpannSysteme [Page]([https://spannsysteme.shop/kategorie/3d-print/ratrig])

    A customer, a friend and a serious pro :)
    
 -Dan Cernogorsky [Page](https://www.printables.com/@DanCernogorsky)

    A customer, a friend with a nice touch on design :)

More extensive credit can be found here: https://www.brs-engineering.com https://www.brs-engineering.com/Oldham.html

[Back to Main Page](/readme.md)

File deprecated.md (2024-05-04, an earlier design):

# LEGACY DEPRECATED PARTS
## -/ Z SYSTEM 1.0

- Z-Ballscrews-upgrade 1
High precision Z system with anti-wobble system 

Version|Description|ReleaseDate|CAD|Thingiverse|Documentation|License|Order
-------------|-----------|-----------|-----------|------------|------------|-----------|-----------
**V1.6**|<br> Last version available. Holes added to access the NEMA17 screws for tuning alignment |29/09/21|[STEP](https://drive.google.com/file/d/1DvUyMbXhosZOEtiP2zKSWmIGoYd-C9qh/view?usp=sharing)| [STL](https://www.thingiverse.com/thing:4978199) || except wings design
**V1.96a**|<br> Documentation links implementation |11/03/22|||[Manuals](https://github.com/FlorentBroise/BRS-Printers-Mod/tree/main/manuals)| except wings design|[SHOP](https://www.brs-engineering.com/Vcore.html)
**V1.96b**|<br> Wings coupling DEPRECATED, Oldham to be installed|18/04/22|||||[SHOP](https://www.brs-engineering.com/Vcore.html)
**V1.97a**|<br> Last version available. Geometry Updated for lighter parts / compatible VC3.0/3.1 (same assembly method) |19/04/22|[ZIP](https://github.com/FlorentBroise/BRS-Printers-Mod/tree/main/cad/1-97a.zip)| |||[SHOP](https://www.brs-engineering.com/Vcore.html)

## -/ Z SYSTEM 2.0

- Z-Ballscrews-upgrade 2
High precision Z system with anti-wobble system 

Version|Description|ReleaseDate|CAD|STL|Documentation|License|Order
-------------|-----------|-----------|-----------|------------|------------|-----------|-----------
**V2.0a Heavy Duty 1204 EXTENDED**|<br>SFU1204 Version - Extend the Z distance of 50mm (need  50mm longer ballscrews spindles), available for 0-2-3-4mm underplates otherwise through height modualator. Corner completly reinforced and high ability, keep the frame aligned from the spindle Axis, use the same Arms, Oldham and Retainer than previous Z upgrade version. Compatible  NEMA17 and NEMA23. Need a clearance bellows the frame, Compatible with every VCore 3.x machines,.|16/01/23| Outdated | Outdated 22| / ||[SHOP](https://store.brs-engineering.com/products/z-upgrade-2-0-vcore-3-x)
**V2.05a Heavy Duty 1204 EXTENDED**|First revision, correcting few CAD errors, some optimisations. [PATCH-NOTE](https://github.com/FlorentBroise/BRS-Printers-Mod/tree/main/patch/BRSZU205aPN.pdf)|20/02/23| /| / | [MANUAL](/manuals/manual2EN.pdf)/ [Troubleshoot](/manuals/TroubleshootingZ.pdf) ||[SHOP](https://store.brs-engineering.com/products/z-upgrade-2-0-vcore-3-x)
**V2.06a Heavy Duty 1204 EXTENDED**|Second revision, correcting few CAD errors, some optimisations. [PATCH-NOTE](https://github.com/FlorentBroise/BRS-Printers-Mod/tree/main/patch/BRSZU206aPN.pdf)|06/03/23| [STEP](https://github.com/FlorentBroise/BRS-Printers-Mod/raw/main/cad/Z-upgrade-2-06a.zip)| / | [MANUAL](/manuals/manual2EN.pdf)/ [Troubleshoot](/manuals/TroubleshootingZ.pdf) ||[SHOP](https://store.brs-engineering.com/products/z-upgrade-2-0-vcore-3-x)
**1204 POS2 ARMS**|<br>SFU1204 Version - Allow to be mounted with the 3.1 rails positions (rear of the front Z 3030). Opening the ZU1.x and 2.0a to the Official Ratrig 2.0 Enclosure kit.|20/02/23| [STEP](https://github.com/FlorentBroise/BRS-Printers-Mod/raw/main/cad/ARM31.step) | / | / ||
**V2.0b Heavy Duty 1605 EXTENDED**|<br>SFU1605 Version (! need of MGN12H carriage !)|04/02/23| [STEP](https://github.com/FlorentBroise/BRS-Printers-Mod/raw/main/cad/Z-Upgrade-2.0b.zip) | / | / ||[SOON]
**V2.05b Heavy Duty 1204 EXTENDED**|First revision, correcting few CAD errors, some optimisations.|22/02/23| [STEP] | / | / ||[SHOP](https://store.brs-engineering.com/products/z-upgrade-2-0-vcore-3-x)
**V2.05b ZU2.x 3mm Spacer**|  A spacer to be used if no enclosure bottom plate is placed.|08/05/23| [3MF](https://github.com/FlorentBroise/BRS-Printers-Mod/raw/main/cad/3mmSPACER.3mf) | / | / ||[SHOP](https://store.brs-engineering.com/products/z-upgrade-2-0-vcore-3-x)
**V2.05b ZU2.x 75mm Feet v1.1**| 1st revision with the T slider a bit reduced to 10mm to let the space for some M6 screws|15/06/23| [STEP](https://github.com/FlorentBroise/BRS-Printers-Mod/raw/main/cad/ZUfeet2.step) | | / ||[SHOP](https://store.brs-engineering.com/products/pieds-x4-pour-vcore-3)
**V2.06a Heavy Duty 1204 3.1 Top**|Add a safety bumper for the MGN carriage|05/07/23| [STEP](https://github.com/FlorentBroise/BRS-Printers-Mod/raw/main/cad/BRS-Open-Front-31.zip) | | / ||[SHOP](https://store.brs-engineering.com/products/z-upgrade-2-0-vcore-3-x)
**V2.7a Heavy Duty 1204 3.1 Simple**| <br>SFU1204 Version - direct adaptation on a stock VC3.1 with the footprints of the bottom plates conserved! You can directly assemble it by swaping the stock Leadcrew pillars with the Ballscrew version. This 2.7th version is basically the same, buth the base block Geometry! ONLY FOR 1204 Ballscrews|29/10/23|[STEP](https://drive.google.com/file/d/1i3fC8A2Sot7tyuvSnKsozXAluxPpP1m1/view?usp=sharing) | | / ||[SHOP](https://store.brs-engineering.com/products/z-upgrade-2-0-vcore-3-x)
**V2.055a Heavy Duty 1204/1605 3.1 Top**|Replace the top front section with the ballscrew top retainer for the new VCORE 3.1 idler plates. Available for stock M5 screw and Precision shoulder bolt. Replace the old stock ZU2.0 BRS open front design since the 04/07/23|04/07/23| / | | / ||[SHOP](https://store.brs-engineering.com/products/z-upgrade-2-0-vcore-3-x)
**V2.056a Heavy Duty 1204/1605 3.1 Top**|FIX an distance issue in the part|22/09/23| [STEP](https://github.com/FlorentBroise/BRS-Printers-Mod/raw/main/cad/BRS-Open-Front-v3.zip) | | / ||[SHOP](https://store.brs-engineering.com/products/z-upgrade-2-0-vcore-3-x)

Version|Description|ReleaseDate|CAD|Thingiverse|License
-------------|-----------|-----------|-----------|------------|-----------
**V1.0**| |12/01/22|| [Link](https://www.thingiverse.com/thing:5197235) |

- Z axis Oldham Join ( New Revision from the December 2021)

Version|Description|ReleaseDate|CAD|Files|License|Order
-------------|-----------|-----------|-----------|------------|-----------|-----------
**V2.2a**|<br>  A Oldham kinematic ring design, More precise, more accurate. |01/01/22|[STEP](https://drive.google.com/file/d/1Um32c3vZ82SMlC5ylu9X6IunsmtLvtSH/view?usp=sharing)| [STL](https://drive.google.com/file/d/11setQH1OrWtbLpgV7RBNb5VHLEKnbiXl/view?usp=sharing)||[SHOP](https://www.brs-engineering.com/Oldham-kit.html)
**V2.2b**|Central unified ring for light bed|09/09/22|[STEP](https://github.com/FlorentBroise/BRS-Printers-Mod/raw/main/cad/RingUnifiedv2.step)|||[SHOP](https://www.brs-engineering.com/Oldham-kit.html)
**V3.0a**|A Oldham kinematic ring redesign for SFU1605 with custom Z system.  |To come||||[SHOP](https://www.brs-engineering.com/Oldham-kit.html)

## 1 UltraLight Gantry XY v1 (DEPRECATED)

Version|Description|ReleaseDate|CAD|Files|License
-------------|-----------|-----------|-----------|------------|------------
**va2.6**(DEPRECATED)| DEPRECATED because of the belt tension forcing the crossbar to bend a bit after few months) <br> |Jan 2022|||
**v2.7**(DEPRECATED)| Adding of Shoulder bolt solution on the whole Gantry <br> |Dec 2021|

## 2 BRSVS High volume cooling solution (DEPRECATED)
High CFM Laminar cooling solution to remove fans from the head, giving more cooling power (PLA) and less weight for the toolhead

Version|Description|ReleaseDate|CAD|Thingiverse|License
-------------|-----------|-----------|-----------|------------|------------
1.2b| <br> |30 Nov 2021| [CAD and Instructions](https://github.com/FlorentBroise/RatRig-Upgrades/blob/main/BRSVS.md) || 

## 3 Flathead v1 Ecosystem (DEPRECATED and replaced by the V2)
A toolhead where the hotend can be swapped at will, within 30sec, without loosing belt tension, and get versatility to adapt your needs in materials!

Version|Description|ReleaseDate|CAD|Thingiverse
-------------|-----------|-----------|-----------|------------
**V0.1-Hextrudort**(DEPRECATED)|| Based on the MirageC design from Hevort project|[CAD](/cad/toolheadv2.step)
**V1.1-LGX Mosquito**(DEPRECATED)|| LGX, Mosquito, Carbon fiber PA12 and titanium based head| <br>|/|
**V1.2-LGX-Lite Mosquito(DEPRECATED)|| LGX-lite, Mosquito/| <br>|/|
**V1.1-LGX V6 (DEPRECATED)|| LGX, E3D V6| <br>|/|
**V1.1-LGX Nova (DEPRECATED)|| LGX, Nova| <br>|/|
**V1.1-LGX Takoto (DEPRECATED)|| LGX, Takoto| <br>|/|
**V1.1-LGX Dragon (DEPRECATED)|| LGX, Dragon| <br>|/|
Carbon fiber and titanium based head, tagged as deprecated because of the compatibility with only the Light gantry va2.6. Technically Fonctionnal and adaptable, CAD will release soon | <br>|March 2022|

- FLATHEAD V2 parts (DEPRECATED)
A ultralight mosquito based toolhead, with Crystal geometric shroud face

Version|Description|Details|CAD|Release date|License|Order
-------------|-----------|-----------|-----------|------------|------------|-----------
**V1.21a-LGX-Lite Mosquito**|| Add the shroud for 8mm Inductive probe|  [Files](/cad/geo8.3mf) [BOM](/bom/BOM_Flatheadv2.xlsx)|22/03/22|

## 4 Toolboard (DEPRECATED)
Version|Description|ReleaseDate|Gerber|Thingiverse
-------------|-----------|-----------|-----------|------------
**V0.1-Toolboard**|| A PCB part to deliver a full modularity| <br>|Jan 2022|

## 5 Wings related parts (DEPRECATED)

- Ballscrew arms for Vcore 3 (Wings Version)

Version|Description|ReleaseDate|CAD|Thingiverse|License
-------------|-----------|-----------|-----------|------------|-----------
**V1.0**||12/01/22|| [Link](https://www.thingiverse.com/thing:5275766)| 

## 6 Shoulder-bolt mod precision parts (Replaced by the Active PMB mod)

- Reinforced Motor bracket mod with bearing

Version|Description|ReleaseDate|CAD|License
-------------|-----------|-----------|-----------|-----------
**STB-V1.1**|<br> Right top motor bracket added for the NEMA R, needs a 625ZZ bearing and a 1mm shim (WORKS ONLY with E3D motor, or any nema17 with a minimum of 27mm shaft lenght)|20/11/21|[Left 3MF](https://github.com/FlorentBroise/BRS-Printers-Mod/raw/main/cad/Bracket.3mf) [Right 3MF](https://github.com/FlorentBroise/BRS-Printers-Mod/raw/main/cad/BracketR.zip)|

- Shoulder-bolt mod precision parts

Version|Description|ReleaseDate|CAD|License
-------------|-----------|-----------|-----------|-----------
**SBS-V1.1**|<br> Compatible with the F695-2R - 695zz Pulley conversion|16/03/2022 | [TopL](https://github.com/FlorentBroise/BRS-Printers-Mod/raw/main/cad/top-left.zip) [TopR](https://github.com/FlorentBroise/BRS-Printers-Mod/raw/main/cad/top-right-bearing.zip) [IdlerR](https://github.com/FlorentBroise/BRS-Printers-Mod/raw/main/cad/Idler-L.3mf) [IdlerL](https://github.com/FlorentBroise/BRS-Printers-Mod/raw/main/cad/Idler-R.3mf)|

###ANTI-WOBBLE Flexure system for SFU Ballscrews
A more cost effective way to decouple XY for non straight ballscrews

Product|Status|View|Manual EN|Release date|Shop|CAD|License
-----------------|------|-----------------------------------| :----: |  :---------------: |  :---------------: |  :---------------: | :---------------:
FLEX-P V1.2 (proto designed 10/10/22)|DEPRECATED, does not correct Z specific angle precession deviation|<br> **FLEX-P-V1.2** A decoupling module based on a flexure mechanism for Z-axis on X and Y independantly. It keeps the advantages of the Oldham / Ring system, and decrease the overall cost, and reduce the manufacturing process to the minimum. It decreases the Z space too by beeing more compact than any anti wobble mechanism. Resistances validated to 25kg before degradation. Base thickness of 15mm for a PACF base, can be bigger to satisfy more rigidity on the decoupling motion, or more Z weight tolerances. Will be standard on the BRS-VULCAIN. Actually in proofing|/|03/23|/| |

### BRS-IDEX for VCORE 3.x
IF you dont want to change the motor bracket, (very simple installation) Good for already working machines

Product|Status|View|Manual EN|Release date|Shop Product |Shop CAD|License
-----------------|------|-----------------------------------| :----: |  :---------------: |  :---------------: |  :---------------: |  :---------------:
BRS-IDEX A1.0 (proto designed 01/02/23) |Cancelled|<br> **BRS-IDEX A1.0** A full IDEX mechanism for Vcore 3.x platform, Designed to be compatible with any VCore and most of his mods like Enclosure 2.0, V1, L3ver M1, and many more, WITHOUT having to modify the FRAME||Q3 2024| ||

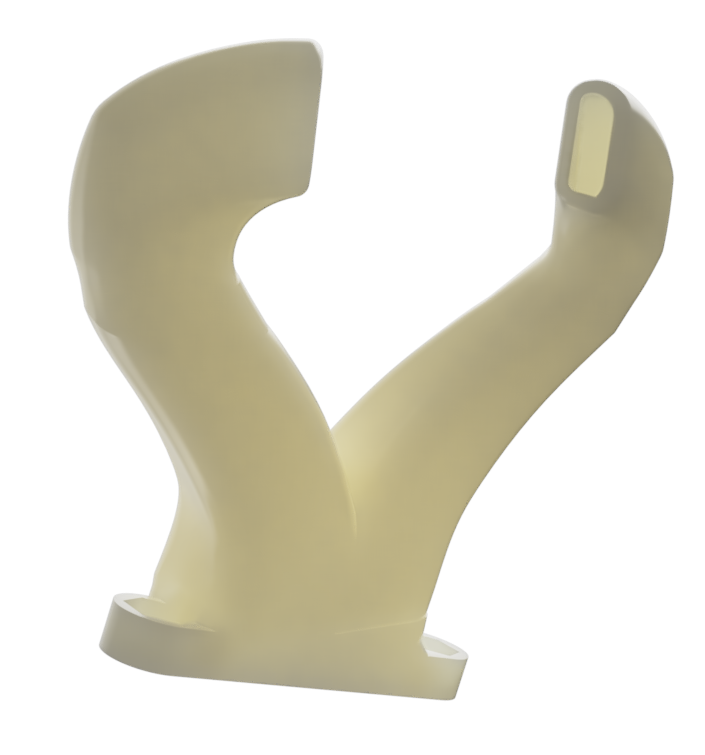
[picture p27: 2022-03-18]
image/Hemera_volc.png

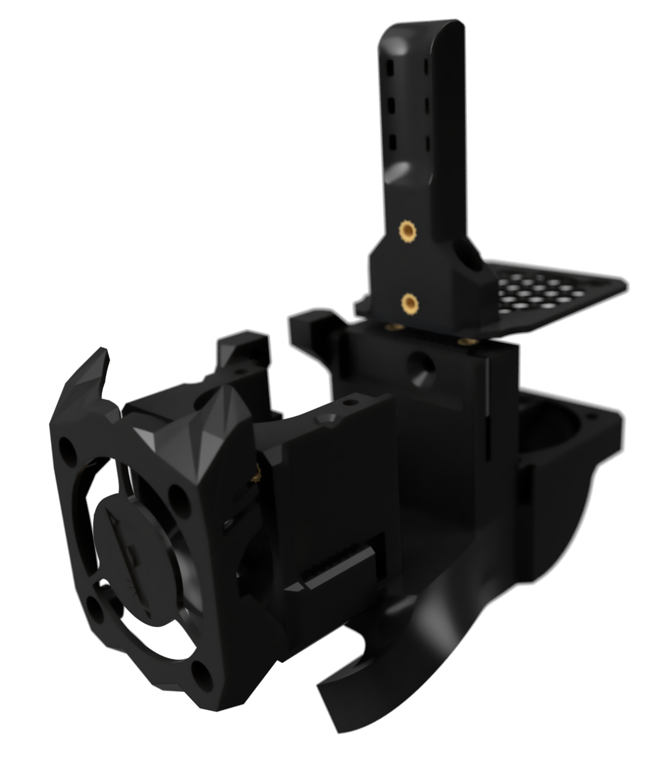
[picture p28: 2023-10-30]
image/RRT.png

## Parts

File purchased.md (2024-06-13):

# BRS-Engineering  
## BOM(Bill Of Material)

In this section you will find the Bill of Material for all upgrades. 

Printer Component|Status|View|STL files|Bill of Material (Excel)
-----------------|------|-----------------------------------| :----: |  :---------------:
BRS-AWD-Drive 1.35|Active|<br> **BRS-AWD-Drive 1.35** ||[Download](https://docs.google.com/spreadsheets/d/1lZiieI_m1PFYK_gN3xTSUbtMcLak3CRZo3O83WT3AfU/edit?usp=sharing)
L3ver M3 AWD 1.0a (Vc3.x with Front 3030)|Active|<br> **L3ver M3 AWD** ||[Download BOM Enclosed](https://docs.google.com/spreadsheets/d/1m4azE54TQerhyBI3S39cNwWqPLjUHiSjp3UHa-RHm1U/edit?usp=sharing)
L3ver M3 AWD 1.0a (Vc3.x without Front 3030)|Active|<br> **L3ver M3 AWD** ||[Download BOM Opened](https://docs.google.com/spreadsheets/d/1Q-RR1Z1-t3DGIQ9Xbndv41vbUf74H0XFt3EJaa1Jg0M/edit?usp=sharing)
Z Upgrade 1.0|Deprecated|**Z-Upgrade 1.x** Ballscrew system|[link](https://www.thingiverse.com/thing:4978199)|[Download](/bom/BOM_ZU_160-165-166.xlsx)  
Z Upgrade 2.0|Deprecated| **Z-Upgrade 2.0** Ballscrew system|/|[Download](/bom/BOM-ZU2.pdf)  
Z Upgrade 2.8a-DE 1204|Active|<br> **Z-Upgrade 2.8** Ballscrew system|/|[Download](https://docs.google.com/spreadsheets/d/1hA8UdFV7IhUFEDgt_LVLpt3l6aZIOX_8x9tYVwdvjZA/edit?usp=sharing)  
Z Upgrade 2.8b-DE 1605|Active|<br> **Z-Upgrade 2.8** Ballscrew system|/|[Download](https://docs.google.com/spreadsheets/d/1QMjidNovDnawUL7VbYypceX7xUfzKQ-BTuSa7OgNYMw/edit?usp=sharing)  
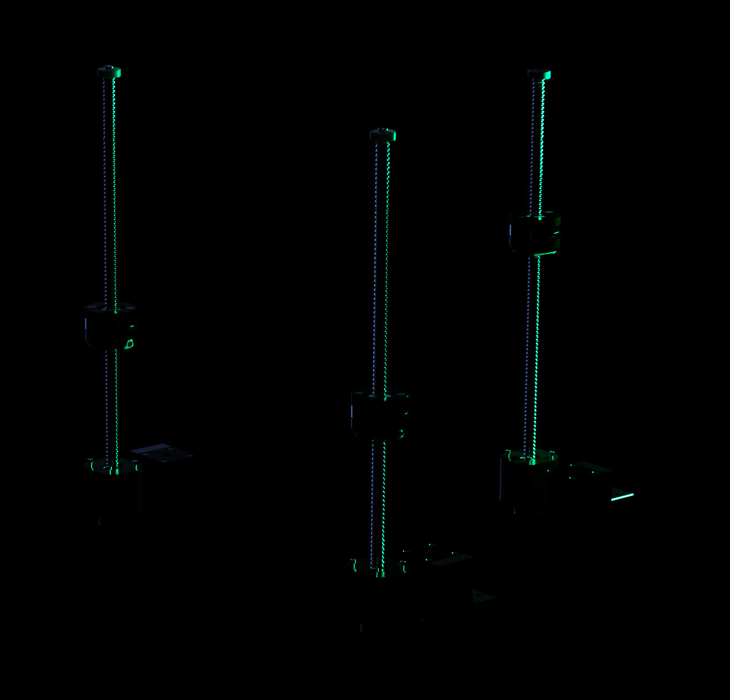
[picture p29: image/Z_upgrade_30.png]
Z Upgrade 3.0 (VCORE4) |Active|<br> **Z-Upgrade 3.0** Ballscrew system|/|[Download]()  
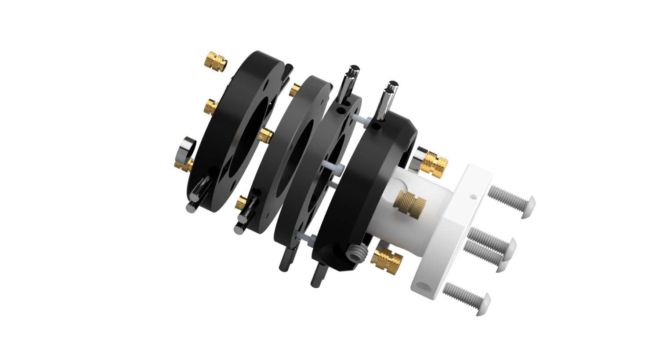
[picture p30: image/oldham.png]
Oldham|Active|<br> **Oldham** Ballscrew system||[Download](/bom/BOM_RINGS-22.pdf)  
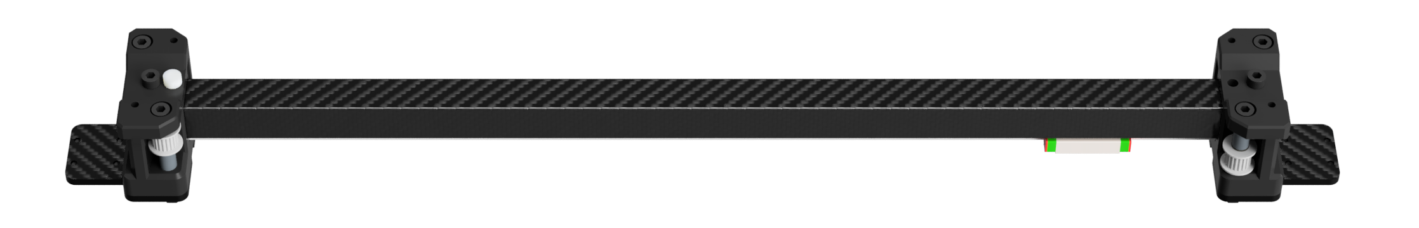
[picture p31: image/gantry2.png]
Ultralight Gantry|Active|<br> **Ultralight Gantry** ||[Download](/bom/BOM.xlsx)  
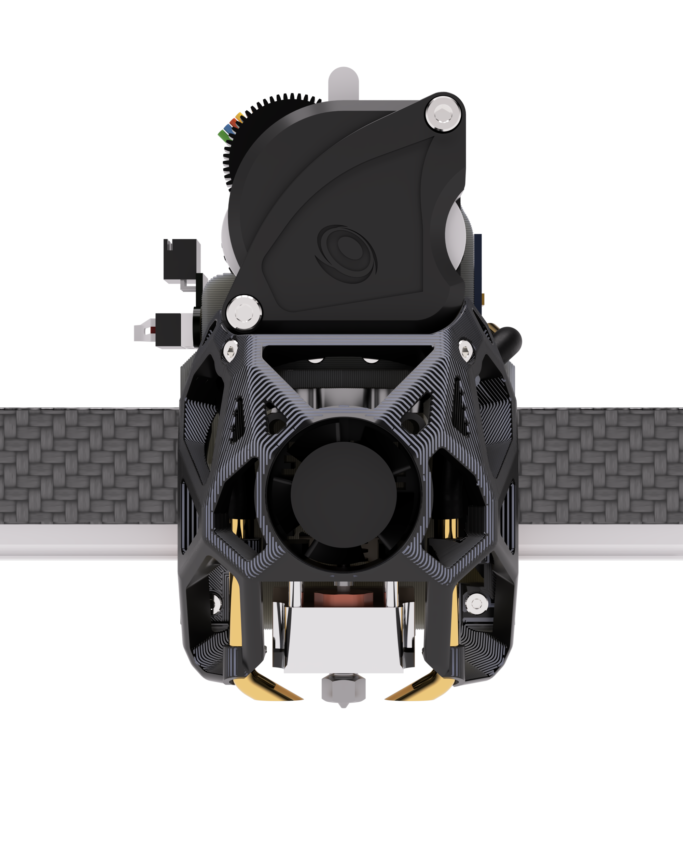
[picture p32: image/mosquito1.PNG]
Flathead V2 toolhead|Active|<br> **Flathead V2 toolhead** ||[Download](/bom/BOM_Flatheadv2.xlsx) 
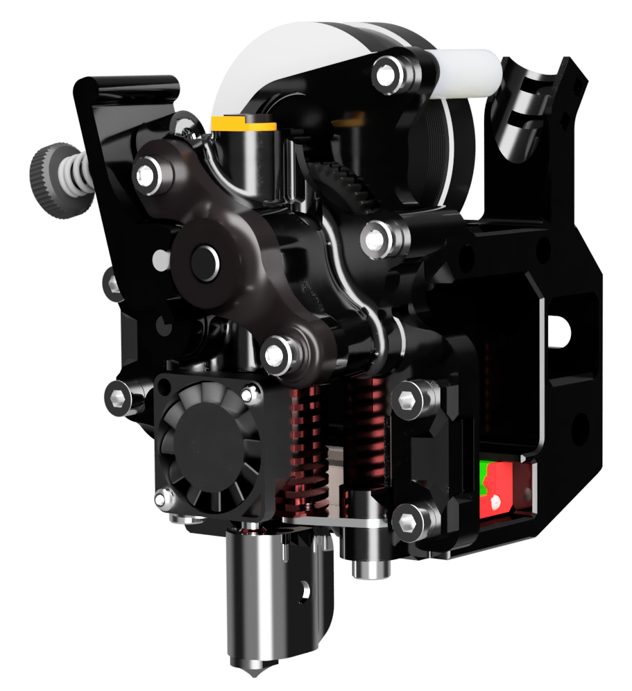
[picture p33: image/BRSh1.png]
BRS-HextrudORT|Beta|<br> **BRS-HextrudORT toolhead** ||[Download soon]() 
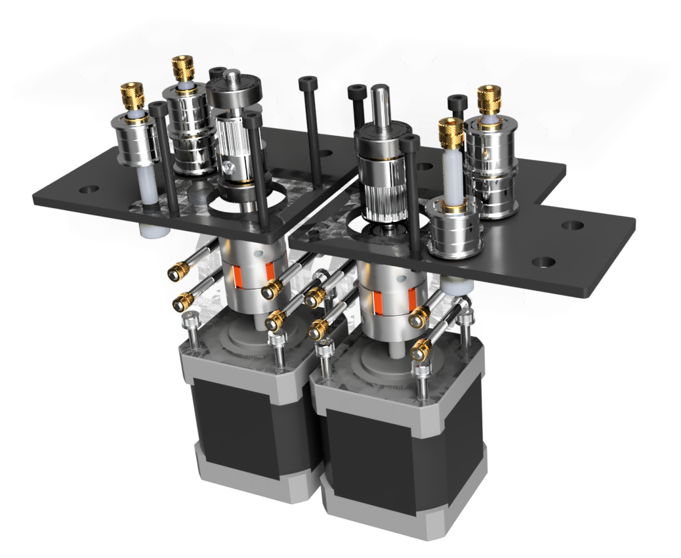
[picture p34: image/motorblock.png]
Precision Modular Motor Blocks|Active|<br> **Precision Modular Motor Block** ||[Download](/bom/BOM_PMH.xlsx) 
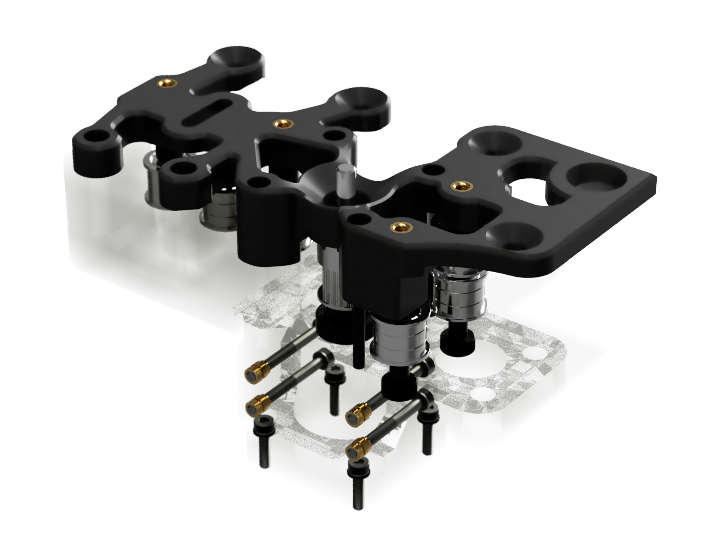
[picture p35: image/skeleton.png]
L3VER M1-M2|Active|<br> **L3VER M1-M2** ||[Download](/bom/BOM-M1-M2.pdf)

## [Back to Main Page](/readme.md)

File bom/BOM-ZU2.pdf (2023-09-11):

ZU 2,0 SFU1204
ITEM | Quantity | note
SFU1204 C7 | 3 | 350-450-550-650-750
BK10 | 2
Chassis M6x12 | 36
Chassis M6x20 | 8
M5x30 | 4
M5x45 | 4
m5x80 | 4
M6 Tnut | 50
M3 Tnut | 5
Cuntersunk M3x8 | 3
M2x8 | 4
M3x40 | 2
m3x10 | 8
M3x15 | 4
M3x30 | 4
M3x20 | 13
M3x35 | 2
Shoulder Bolt D5M4x35 | 2
Microshim 8x5x1 | 10
M6 Washers | 36 | not mandatory
M5 Washers | 8
Insert M4 | 24
Insert M6 | 8 | For Old plate idler layout
Insert M5 | 8
Insert M2 | 4
Insert M3 | 15
Coupler 8x5 (Nema 17) | 3 | For Nema 23, check the shaft size
608-2RS | 3
Magnet 8x3 | 12
Ball bearing 4-6mm | 12
Dowel pin 35mm | 6
Dowel pin 10mm | 48

ZU 2,0 SFU1605
ITEM | Quantity
SFU1605 C7 | 3
BK12 | 2
Chassis M6x12 | 36
Chassis M6x20 | 8
M5x30 | 8
m5x80 | 4
M6 Tnut | 50
M3 Tnut | 5
Cuntersunk M3x8 | 3
M3x5 | 12
M3x40 | 2
m3x10 | 8
M3x15 | 4
M3x30 | 4
M3x20 | 13
M3x35 | 2
Shoulder Bolt D5M4x35 | 2
Microshim 8x5x1 | 10
M6 Washers | 36
M5 Washers | 8
Insert M4 | 4
Insert M6 | 8
Insert M5 | 24
M5x16 | 12
Insert M3 | 18
Coupler 10x5 (NEMA 17) | 3
6000-zz | 3
Magnet 8x3 | 12
Ball bearing 4-6mm | 12
Dowel pin 35mm | 6
Dowel pin 10mm | 48

note
350-450-550-650-750

add +2 if installing new idler plate design

not mandatory

For Old idler plate layout

add +12 if installing Nema23

For NEMA 23 Only

For Nema 23, check the shaft size

10x26x8mm

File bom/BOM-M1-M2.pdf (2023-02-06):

M2
Item | Quantity
Shoulder bolt D5M4x45mm | 2
Shoulder bolt D5M4x35mm | 8
M4 Ruthex Insert | 12
M3 Ruthex Insert | 16
M4x15mm (20mm max) | 4
Countersunk M5x40 | 2
Shim 8x5x1mm | 18
F695 | 12
695zz | 24
M4 washer | 2
M5 washer | 2
Nylstop M4 nut | 2
M5 nut | 2
Cuntersunk M6x14 | 8
M6x16 | 6
T nut M6 | 12
D5x55mm steel axis | 2
Disc coupler 5x5 | 2
Nylstop M5 nut | 2
M3x30 | 8
M3x12 | 8

M1
Item | Quantity
Shoulder bolt D5M4x45mm | 2
Shoulder bolt D5M4x35mm | 3
M4 Ruthex Insert | 3
M5 Ruthex Insert | 2
M5x15-20mm (max) | 2
Countersunk M5x40mm (max) (Lever headless part) | 2
Shim 8x5x1mm | 9
F695 | 12
695zz | 6
M4 washer | 2
M5 washer | 2
Nylstop M4 nut | 2
M5 nut | 2
Countersunk M6x14 | 3
M5x16 | 3
T nut M5 | 3

T nut M6 | 3
Nylstop M5 nut | 2
M5x40 | 3

Info

https://fr.aliexpress.com/item/1005003335259903.html?spm=a2g0o.orde

https://fr.aliexpress.com/item/1005001698010943.html?spm=a2g0o.orde

Info
https://fr.aliexpress.com/item/1005003335259903.html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

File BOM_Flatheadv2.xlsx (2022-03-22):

Thumbnail | Part Name | Description | Print/Buy/Make | QTY | Comment
 | Main part |  | Print/Buy | 1 | 7 perimeters
 | LGX-Lite Holder | Both 20mm or 17mm motors compatible | Print/Buy | 1 | 7 perimeters
 | Lerdge Microswitch |  | Buy/Recycle | 1
 | MGN9H Carriage | Hiwin prefered | Buy | 1
 | Vcore belt graber |  | Print | 2
 | Vcore Belt tensionner 9mm |  | Print | 2
 | LGX Lite | Both 20mm or 17mm motors compatible | Buy | 4
 | Mellow MiniAB |  | Buy | 1
 | ADXL345 OR ADXL345 Mellow | (Adafruit version "non compatible") | Buy | 1
 | Dowel pin | 35mm | Buy | 2 | Add rigidity in the main assembly
 | Mosquito / Magnum / Volcomosq | Volcomosq variation compatible, need a probe adjustment | print | 1
 | M5 Nyloc | Titanium prefered | Buy | 2
 | m3x30 | Titanium prefered |  | 1
 | m3x35 | Titanium prefered |  | 1
 | M5 40mm | Titanium prefered | Buy | 2
 | M2x8 | Titanium prefered | Buy | 6
 | M3x8 | Titanium prefered | Buy | 9
 | Ruthex Insert M2 |  | buy | 6
 | Ruthex Insert M3 |  | buy | 12
 | M3x30 | Titanium prefered | buy | 1
 | M3x10 | Titanium prefered | buy | 14
 | D5x30 Compression spring | Optionnal | buy | 2
 | M3 3mm spacer | can be printed | Print/buy | 2
 | Reinforcer for the Motor | Either for 17 or 20mm motor | print | 1
 | Durit tube (silicon) 3mm ID 5mm OD |  | Buy | 20cm
 | T spliter 4mm/6mm OD | Can be printed and UV resin coated | Buy | 1
 | SE 25mm fan |  | Buy | 1
 | m3x6 | Titanium prefered | buy | 2
 | EUCLID probe |  | Buy | 1
 | Euclid Dock | for Euclid Only | Print | 1
 | std Geo Shroud | Euclid | Print | 1
 | Inductive Geo shroud | 8mm Inductive | Print | 1
 | Duct ends | Brass 3,5mm ID 4mm OD | Make | 2 | Use the tool in the GIT link to bend it

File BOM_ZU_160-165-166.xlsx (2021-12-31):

SubAssy | Category | Item | Thumbnail | Part Name | Part Description | Print/Buy | QTY | Comment | Vendor | Vendor URL
 |  |  |  | SFU1204-400 With Nut | For the Vcore-3-300 | Buy | 3 | BK10 and BF10 machined end required. BK10 required. and BF10 blocks is not. LOOK For C7-G7 Grade |  | https://www.ebay.fr/itm/353302159798
 |  |  |  | SFU1204-500 With Nut | For the Vcore-3-400 | Buy | 3 | BK10 and BF10 machined end required. BK10 required. and BF10 blocks is not. LOOK For C7-G7 Grade |  | https://www.ebay.fr/itm/273908878058?hash=item3fc63dcaea:g:3SQAAOSw2gJfPhH-
ZR_V2.5 | Buy | 3 |  | SFU1204-600 With Nut | For the Vcore-3-500 | Buy | 3 | BK10 and BF10 machined end required. BK10 required. and BF10 blocks is not. LOOK For C7-G7 Grade |  | https://www.ebay.fr/itm/353302159798
ZR_V2.5 | Buy | 4 |  | Ball Bearing 608ZZ | Bearing 608ZZ if not in the BF10 | Buy | 3
 |  |  |  | BK10 + Nut (Angular bearing included) |  | Buy | 3
 |  |  |  | BF10 + circlip + 608ZZ |  | Buy | 2 | NOT Required: the 608ZZ is mandatory
 |  |  |  | Oldham Coupler 5,0-8,0 | (Prefered, but spider coupler type works too) | Buy | 3 | Either Spider or Oldham
ZR_V2.5 | Buy | 7 |  | Coupler D20L25-5.0-8.0 | Coupler, Spider - 8 to 5mm | Buy | 3 | Included with the RR kit |  | https://s.click.aliexpress.com/e/_AVhQZK
ZR_V2.5 | Buy | 9 |  | MGN12H_Rail Assy | MGN12H Rail from the RR kit | Buy | 3 | No need to cut it |  | RR
ZR_V2.5 | Buy | 12 |  | NEMA17 1.8/0.9 degree Stepper Motors 48 mm | Stepper Motor - NEMA17X48mm | Buy | 3 | Even with 500 bed plate, motors should not let the bed falling down due to backdriving |  | E3D / Trianglelab / LDO
ZR_V2.5 | Hardware | 13 |  | Ball_Bearing_6mm | Bearing, Ball - 6mm | Buy | 9 | Ball Bearing dont need to be magnetized, Chrome Steal preffered. 7mm or 8mm can be tested to decouple the system and tune it |  | https://www.amazon.fr/gp/product/B00J8JR03O/ref=ppx_yo_dt_b_asin_title_o07_s00?ie=UTF8&psc=1
ZR_V2.5 | Hardware | 14 |  | Magnet_8X3mm | Magnet, Disc - 8X3mm | Buy | 30 | Neodymium (these magnets are sold as 3mm thick but the ones received are 2.75mm. True 3mm thick will not create any issue.) | Amazon | https://www.amazon.fr/gp/product/B074C79DJS/ref=ppx_yo_dt_b_asin_title_o03_s00?ie=UTF8&psc=1
ZR_V2.5 | Hardware | 18 |  | M4_Nut_94150A335 | Nut, Hex - M4 | Buy | 9 |  |  | Any shop near your location ;)
ZR_V2.5 | Hardware | 24 |  | M3x35_ButtonHeadScrew_91239A326 | Screw, Button Head - M3x35 | Buy | 11
ZR_V2.5 | Hardware | 25 |  | M6x12_ButtonHeadScrew_97763A820 | Screw, ButtonHead - M6x12mm | Buy | 14
ZR_V2.5 | Hardware | 26 |  | M6x20_ButtonHeadScrew_91239A228 | Screw, ButtonHead - M6x20mm | Buy | 15
 |  |  |  | M3x4(5) Countersink screw |  | Buy | 3
ZR_V2.5 | Hardware | 27 |  | M6X14_ButtonHeadScrew_92095A227 | Screw, ButtonHead - M6X14mm | Buy | 16
ZR_V2.5 | Hardware | 28 |  | M3X10_CapScrew_92290A115 | Screw, Cap - M3X10mm | Buy | 8
ZR_V2.5 | Hardware | 29 |  | M3X12_CapScrew_92290A117 | Screw, Cap - M3X12mm | Buy | 18
ZR_V2.5 | Hardware | 30 |  | M5x40_CapScrew_92290A118 | Screw, Cap - M5X40 | Buy | 4
ZR_V2.5 | Hardware | 33 |  | M4X20_CapScrew_92290A150 | Screw, Cap - M4X20mm | Buy | 9
 |  |  |  | M6x60 CapScrew | Screw, Cap - M6X60 |  | 2
ZR_V2.5 | Hardware | 34 |  | M5X30_CapScrew_90605A257 | Screw, Cap - M5X30 | Buy | 12
ZR_V2.5 | Hardware | 35 |  | M2x8_CapScrew_91290A434 | Screw, CapScrew - M2x8 | Buy | 4
 |  |  |  | Arm R |  | Print | 1
 |  |  |  | Arm L |  | Print | 1
 |  |  |  | Arm B |  | Print | 1
 |  |  |  | Retainer R |  | Print | 1
 |  |  |  | Retainter L |  | Print | 1
 |  |  |  | Retainer B |  | Print | 1
 |  |  |  | Bracket R |  | Print | 1
 |  |  |  | Bracket L |  | Print | 1
 |  |  |  | Bracket B |  | Print | 1
 |  |  |  | Wing low |  | Print | 3
 |  |  |  | Wing top |  | Print | 2
 |  |  |  | Wing top mirrored |  | Print | 1
 |  |  |  | Ruthex Insert M5 |  | buy | 12
 |  |  |  | Ruthex Insert M3 |  | buy | 16(4)
 |  |  |  | Ruthex Insert M2 |  | buy | 4

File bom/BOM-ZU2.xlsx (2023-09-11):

ZU 2,0 SFU1204 |  |  | ZU 2,0 SFU1605
ITEM | Quantity | note | ITEM | Quantity | note
SFU1204 C7 | 3 | 350-450-550-650-750 | SFU1605 C7 | 3 | 350-450-550-650-750
BK10 | 2 |  | BK12 | 2
Chassis M6x12 | 36 |  | Chassis M6x12 | 36
Chassis M6x20 | 8 |  | Chassis M6x20 | 8
M5x30 | 4 |  | M5x30 | 8
M5x45 | 4
m5x80 | 4 |  | m5x80 | 4
M6 Tnut | 50 |  | M6 Tnut | 50
M3 Tnut | 5 |  | M3 Tnut | 5
Cuntersunk M3x8 | 3 |  | Cuntersunk M3x8 | 3
M2x8 | 4 |  | M3x5 | 12 | add +2 if installing new idler plate design
M3x40 | 2 |  | M3x40 | 2
m3x10 | 8 |  | m3x10 | 8
M3x15 | 4 |  | M3x15 | 4
M3x30 | 4 |  | M3x30 | 4
M3x20 | 13 |  | M3x20 | 13
M3x35 | 2 |  | M3x35 | 2
Shoulder Bolt D5M4x35 | 2 |  | Shoulder Bolt D5M4x35 | 2
Microshim 8x5x1 | 10 |  | Microshim 8x5x1 | 10
M6 Washers | 36 | not mandatory | M6 Washers | 36 | not mandatory
M5 Washers | 8 |  | M5 Washers | 8
Insert M4 | 24 |  | Insert M4 | 4
Insert M6 | 8 | For Old plate idler layout | Insert M6 | 8 | For Old idler plate layout
Insert M5 | 8 |  | Insert M5 | 24 | add +12 if installing Nema23
Insert M2 | 4 |  | M5x16 | 12 | For NEMA 23 Only
Insert M3 | 15 |  | Insert M3 | 18
Coupler 8x5 (Nema 17) | 3 | For Nema 23, check the shaft size | Coupler 10x5 (NEMA 17) | 3 | For Nema 23, check the shaft size
608-2RS | 3 |  | 6000-zz | 3 | 10x26x8mm
Magnet 8x3 | 12 |  | Magnet 8x3 | 12
Ball bearing 4-6mm | 12 |  | Ball bearing 4-6mm | 12
Dowel pin 35mm | 6 |  | Dowel pin 35mm | 6
Dowel pin 10mm | 48 |  | Dowel pin 10mm | 48

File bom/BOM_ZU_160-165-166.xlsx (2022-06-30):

SubAssy | Category | Item | Thumbnail | Part Name | Part Description | Print/Buy | QTY
 |  |  |  | SFU1204-400 With Nut | For the Vcore-3-300 | Buy | 3
 |  |  |  | SFU1204-500 With Nut | For the Vcore-3-400 | Buy | 3
ZR_V2.5 | Buy | 3 |  | SFU1204-600 With Nut | For the Vcore-3-500 | Buy | 3
ZR_V2.5 | Buy | 4 |  | Ball Bearing 608ZZ | Bearing 608ZZ if not in the BF10 | Buy | 3
 |  |  |  | BK10 + Nut (Angular bearing included) |  | Buy | 3
 |  |  |  | BF10 + circlip + 608ZZ |  | Buy | 2
 |  |  |  | Oldham Coupler 5,0-8,0 | (Prefered, but spider coupler type works too) | Buy | 3
ZR_V2.5 | Buy | 7 |  | Coupler D20L25-5.0-8.0 | Coupler, Spider - 8 to 5mm | Buy | 3
ZR_V2.5 | Buy | 9 |  | MGN12H_Rail Assy | MGN12H Rail from the RR kit | Buy | 3
ZR_V2.5 | Buy | 12 |  | NEMA17 1.8/0.9 degree Stepper Motors 48 mm | Stepper Motor - NEMA17X48mm | Buy | 3
ZR_V2.5 | Hardware | 13 |  | Ball_Bearing_6mm | Bearing, Ball - 6mm | Buy | 9
ZR_V2.5 | Hardware | 14 |  | Magnet_8X3mm | Magnet, Disc - 8X3mm | Buy | 30
ZR_V2.5 | Hardware | 18 |  | M4_Nut_94150A335 | Nut, Hex - M4 | Buy | 9
ZR_V2.5 | Hardware | 24 |  | M3x35_ButtonHeadScrew_91239A326 | Screw, Button Head - M3x35 | Buy | 11
ZR_V2.5 | Hardware | 25 |  | M6x12_ButtonHeadScrew_97763A820 | Screw, ButtonHead - M6x12mm | Buy | 14
ZR_V2.5 | Hardware | 26 |  | M6x20_ButtonHeadScrew_91239A228 | Screw, ButtonHead - M6x18mm | Buy | 15
 |  |  |  | M3x4(5) Countersink screw |  | Buy | 3
ZR_V2.5 | Hardware | 27 |  | M6X14_ButtonHeadScrew_92095A227 | Screw, ButtonHead - M6X14mm | Buy | 16
ZR_V2.5 | Hardware | 28 |  | M3X10_CapScrew_92290A115 | Screw, Cap - M3X10mm | Buy | 8
ZR_V2.5 | Hardware | 29 |  | M3X12_CapScrew_92290A117 | Screw, Cap - M3X12mm | Buy | 18
ZR_V2.5 | Hardware | 30 |  | M5x40_CapScrew_92290A118 | Screw, Cap - M5X40 | Buy | 4
ZR_V2.5 | Hardware | 33 |  | M4X20_CapScrew_92290A150 | Screw, Cap - M4X20mm | Buy | 9
 |  |  |  | M6x60 CapScrew | Screw, Cap - M6X55 |  | 2
ZR_V2.5 | Hardware | 34 |  | M5X30_CapScrew_90605A257 | Screw, Cap - M5X30 | Buy | 12
ZR_V2.5 | Hardware | 35 |  | M2x8_CapScrew_91290A434 | Screw, CapScrew - M2x8 | Buy | 4
 |  |  |  | Arm R |  | Print | 1
 |  |  |  | Arm L |  | Print | 1
 |  |  |  | Arm B |  | Print | 1
 |  |  |  | Retainer R |  | Print | 1
 |  |  |  | Retainter L |  | Print | 1
 |  |  |  | Retainer B |  | Print | 1
 |  |  |  | Bracket R |  | Print | 1
 |  |  |  | Bracket L |  | Print | 1
 |  |  |  | Bracket B |  | Print | 1
 |  |  |  | Wing low |  | Print | 3
 |  |  |  | Wing top |  | Print | 2
 |  |  |  | Wing top mirrored |  | Print | 1
 |  |  |  | Ruthex Insert M5 |  | buy | 12
 |  |  |  | Ruthex Insert M3 |  | buy | 16(4)
 |  |  |  | Ruthex Insert M2 |  | buy | 4
 |  |  |  | M6 Washers |  | buy | 20+

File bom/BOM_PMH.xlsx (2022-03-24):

Thumbnail | Part Name | Description | Print/Buy/Make | QTY | Comment
 | Ball Bearing F695 |  | Buy | 12
 | Ball Bearing 625ZZ |  | Buy | 4
 | Shoulder Bolt D5 m4 35mm |  | Buy | 4
 | D5 1mm Shim |  | Buy | 10
 | 695zz Bearing |  | Buy | 6
 | XY Top Left |  | Buy | 1
 | Motor Clamp |  | Print | 2 | 7 perimeter 25% infill (PACF)
 | Left holder |  | Print | 1
 | Right holder |  | print | 1
 | XY Top Right |  | Buy | 1
 | Rubber Coupler / Disk coupler | 5x5 / FOR MOTION, NOT TORQUE | Buy | 2
 | Stock plates |  | Buy | 2
 | Ruthex Insert M4 |  | buy | 4
 | Ruthex Insert M3 |  | buy | 16
 | M3x30 |  | buy | 8
 | M3x12 |  | buy | 8
 | M3 Whasher |  | buy | 8
 | Axe 5mm +-55mm | take a longer one and cut it to the desired lenght | buy | 2

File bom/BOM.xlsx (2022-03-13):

Thumbnail | Part Name | Description | Print/Buy/Make | QTY | Comment
 | Spacer |  | Buy | 4
 | Carbon Fiber tube 20x20x18 | V300:422mm V400:522mm V500:622mm | Buy | 1
 | Ball Bearing F695 |  | Buy | 8
 | Ball Bearing 695 |  | Buy | 4
 | Shoulder Bolt D5 m4 45mm |  | Buy | 4
 | D5 1mm Shim |  | Buy | 8
 | M5 Flanged Nut | Titanium prefered | Buy | 4
 | MGN9H Rail + Carriage | V300:400mm V400:500mm V500:600mm | Buy | 1
 | Clamp | To maintain the CF tube uncrushed, a bit bigger than the tube, you need to sand it a bit to a perfect pressfit | Print | 2 | House a m5 flange nut, print at 100% infill
 | Left Joiner |  | Print | 1 | Redesigned to raise the rigidity and does not rely on the shoulder bolt to support all the structural tensions
 | Right Joiner |  | print | 1 | Redesigned to raise the rigidity and does not rely on the shoulder bolt to support all the structural tensions
 | M4 Nyloc | Titanium prefered | Buy | 4
 | M5 55mm | Titanium prefered | Buy | 2
 | M50x20 | Titanium prefered | Buy | 2
 | M3x10 | Titanium prefered | Buy | 13
 | Plates | Carbon fiber prefered (4mm) | buy/Make | 2 | DXF Included (L and R ARE DIFFERENT)
 | Ruthex Insert M3 |  | buy | 4
 | M3x10 | Titanium prefered | buy | 14
 | M3 nut | Titanium prefered | buy | 14
 | M3 Whasher | Titanium prefered | buy | 14

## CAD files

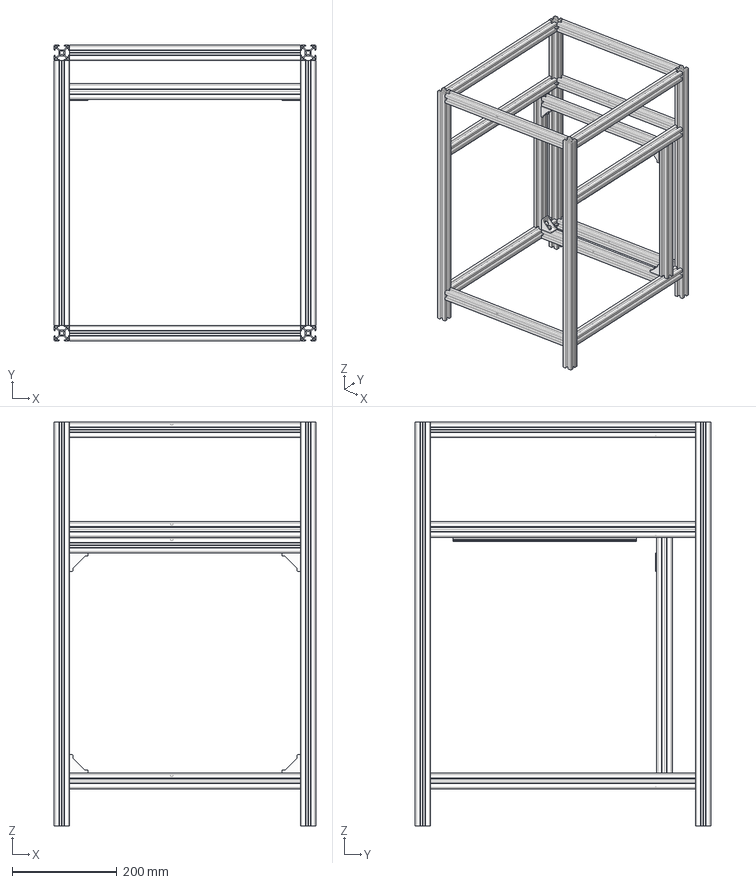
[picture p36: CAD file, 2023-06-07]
cad/Vulcain-Frame-Assembly.step
500.0 x 565.0 x 771.0 mm
T-Slot 3030 - Black - 505mm (Broken) v1 x 6
T-Slot 3030 - Black - 700mm v1 x 4
T-Slot 3030 - Black - 440mm v1 x 7
T-Slot 3030 - Black - 450mm v1 x 2
T-Slot 3030 - Black - 420mm v1
Cast 90 Degree Corner Bracket for 3030 - 6 Slot - Black v1 x 4
Washer Simple M6 v1 x 8
Cap Head Screw M6x12 v1 x 8
T-Nut - Drop In for 3030 - M6 v1 x 8
Linear Rail - MGN12 350mm + MGN12C carriage v1 x 2
Cap Head Screw M3x12 v1 x 28
T-Nut - Drop In for 3030 - M3 v1 x 28

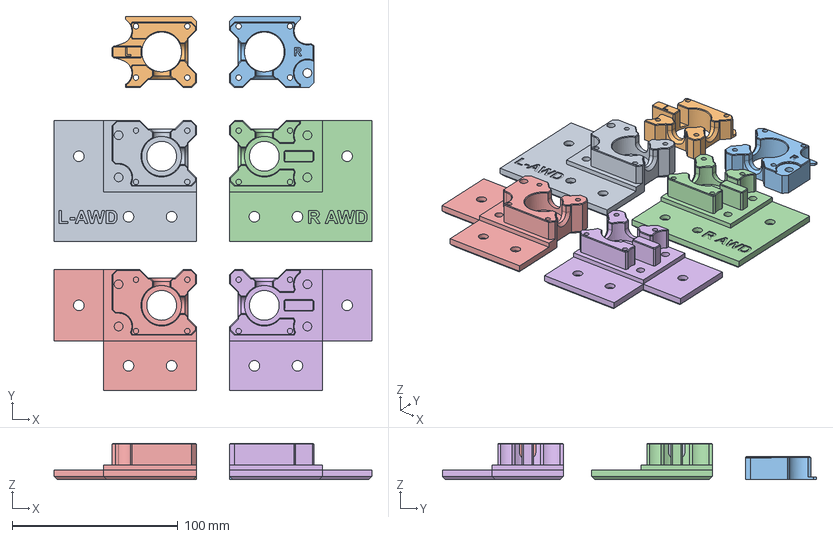
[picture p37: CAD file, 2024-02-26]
cad/BRS-AWD-stock.step
192.0 x 226.0 x 22.0 mm
xy_motor_cage_top_L
xy_motor_cage_bottom_L
xy_motor_cage_bottom_R
xy_motor_cage_top_R
xy_motor_cage_top_L (1)
xy_motor_cage_top_R (1)

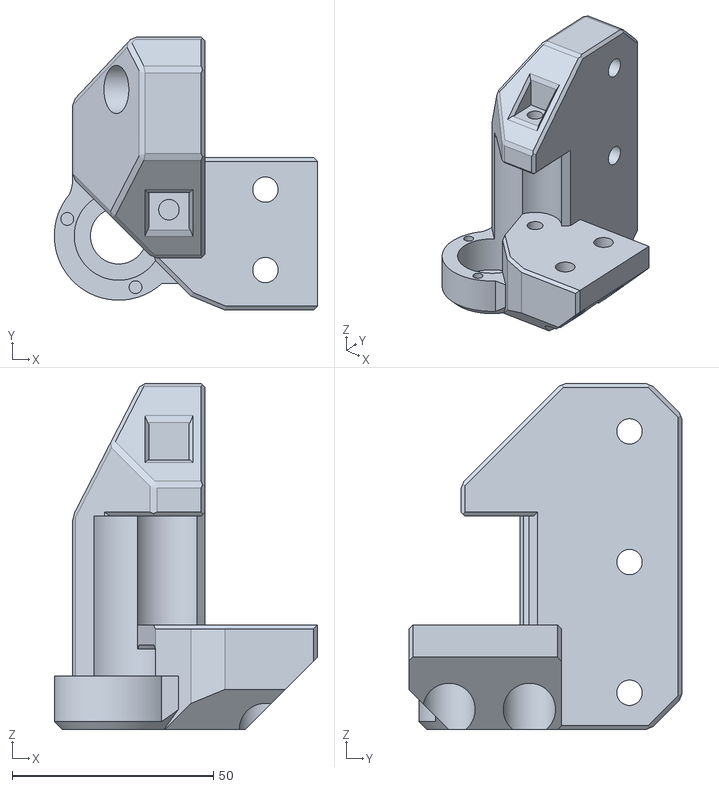
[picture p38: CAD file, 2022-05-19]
cad/stl/OFL.stl
65.5 x 68.0 x 86.0

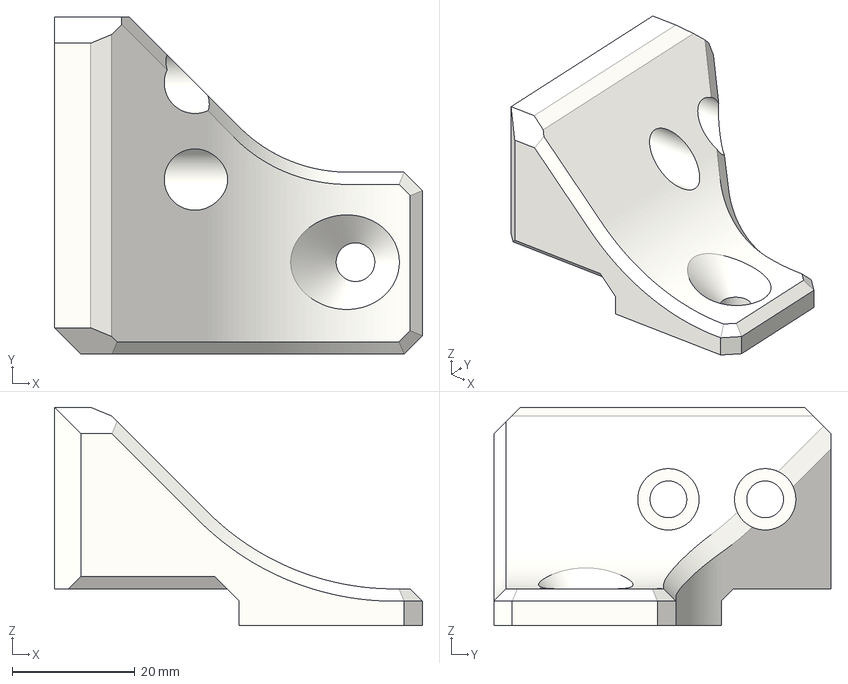
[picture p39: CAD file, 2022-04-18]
Enclosure_bracket.3mf
60.0 x 55.0 x 35.6 mm

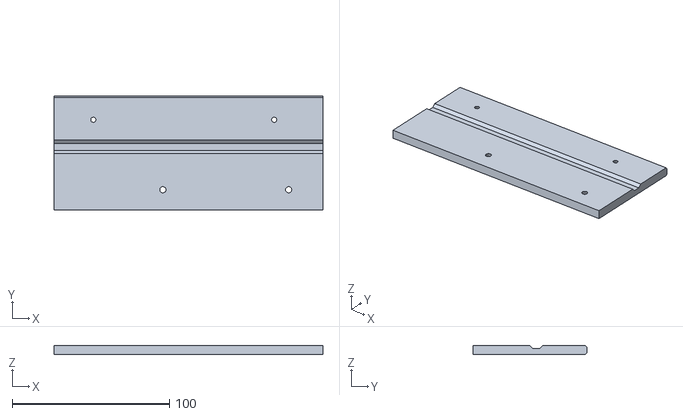
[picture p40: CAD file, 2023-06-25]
stl/m1-plates/400/M1Refresh/Rear L.stl
171.1 x 72.3 x 6.00

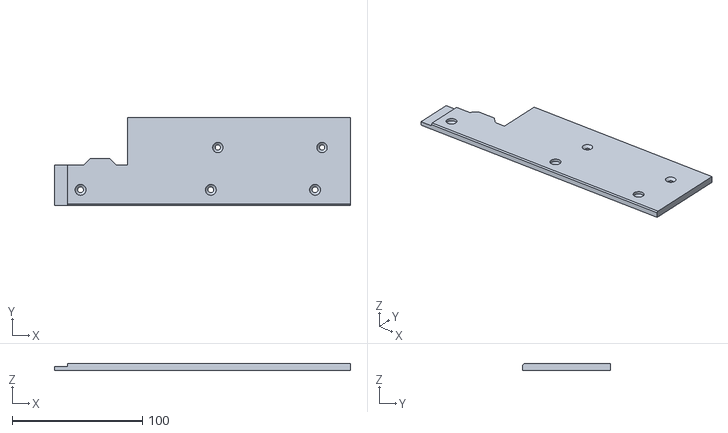
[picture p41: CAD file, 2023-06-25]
stl/m1-plates/400/M1Refresh/top L.stl
227.2 x 67.5 x 5.00

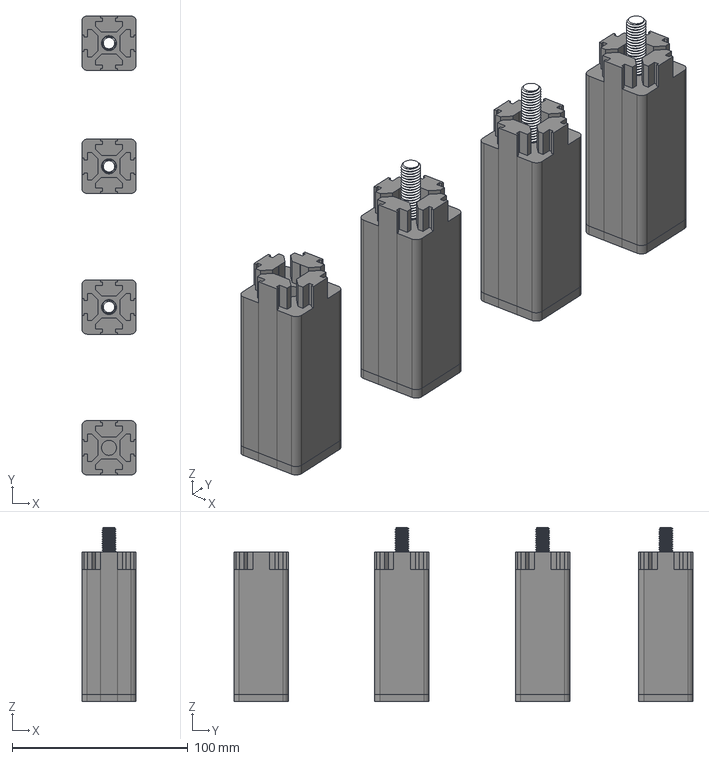
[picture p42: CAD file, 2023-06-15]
cad/ZUfeet2.step
30.9 x 260.9 x 99.0 mm
Composant3 x 4
91290A210_Alloy Steel Socket Head Screw x 4

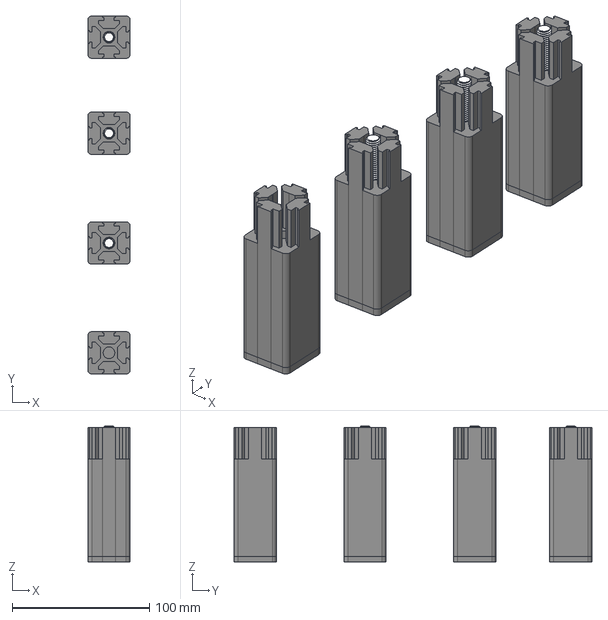
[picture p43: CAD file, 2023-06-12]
cad/ZUfeet.step
30.9 x 260.9 x 99.0 mm
Composant3 x 4
91290A210_Alloy Steel Socket Head Screw x 4

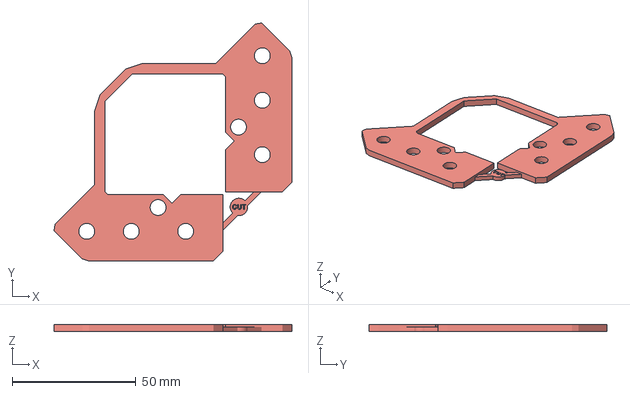
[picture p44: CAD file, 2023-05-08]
cad/3mmSPACER.3mf
96.2 x 96.2 x 3.00 mm

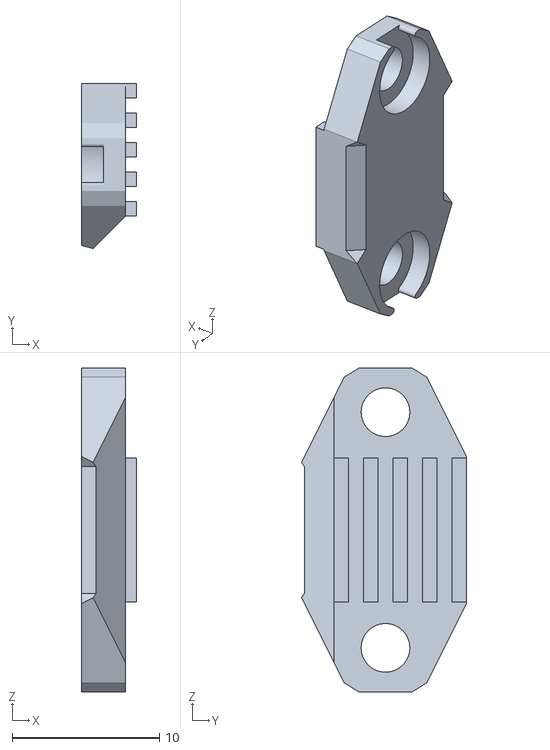
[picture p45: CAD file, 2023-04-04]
cad/Belt-grabber.stl
3.75 x 11.2 x 22.0

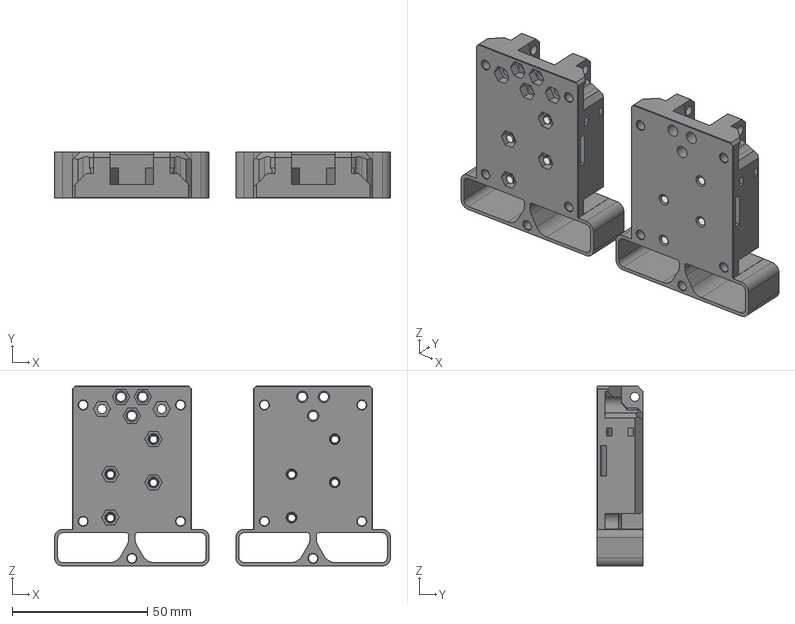
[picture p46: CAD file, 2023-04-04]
cad/EVATLESS.step
124.2 x 17.0 x 66.5 mm
front_universal - face_belt_grabber v1 x 2
front_universal - face_belt_grabber v1 (1) x 2
92095A119_Button Head Hex Drive Screw x 8

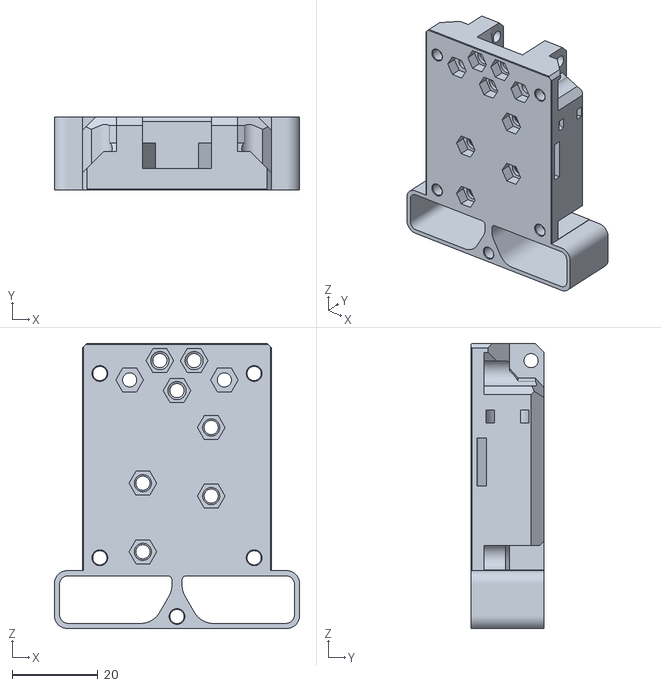
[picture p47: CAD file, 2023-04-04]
cad/EVATLESS-Hex.stl
57.2 x 17.0 x 66.5

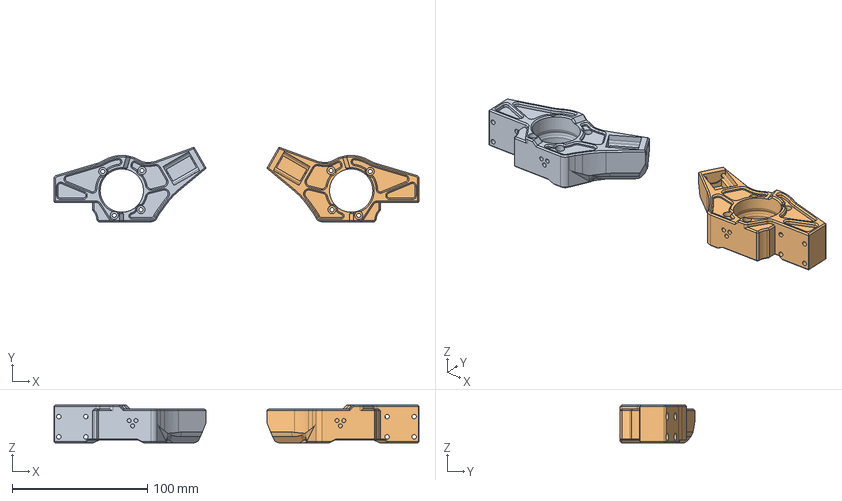
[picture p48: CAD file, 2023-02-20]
cad/ARM31.step
270.0 x 55.2 x 28.0 mm

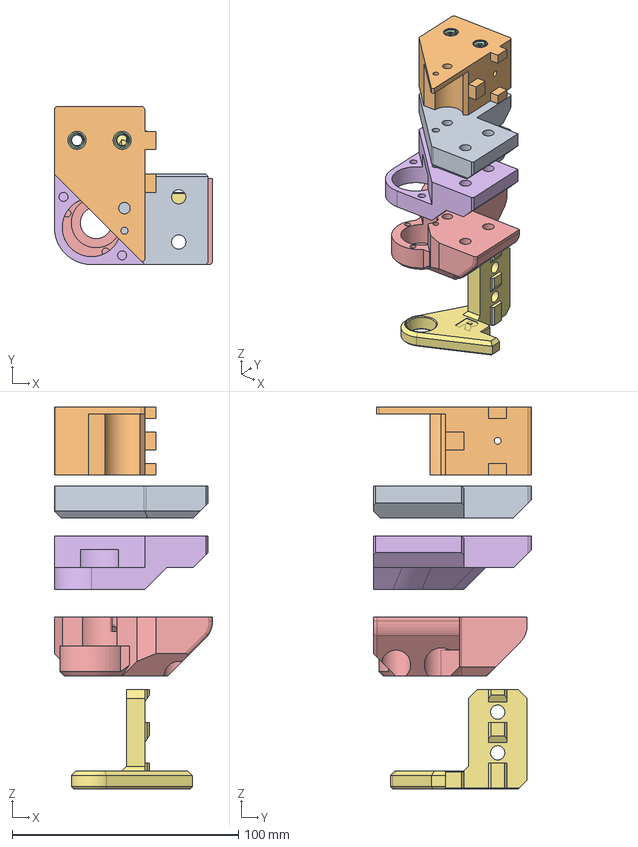
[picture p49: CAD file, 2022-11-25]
cad/BOF2.step
70.0 x 70.0 x 169.0 mm
Composant7
94459A210_Heat-Set Inserts for Plastic x 4
Idler Retainer ZU 1.6-1.99 v1
Retainer SFU1605 VULCAIN PROTO v1
LS retainer stock 3.1
94459A210_Heat-Set Inserts for Plastic (1)

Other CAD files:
cad/stl/OFR.stl
stl/m1-plates/400/M1Refresh/Top R.stl
stl/m1-plates/400/M1Refresh/rear R.stl
cad/EVATLESS-In.stl
cad/ARM-L-165-MKC.3mf
cad/ARM-R-165-MKC.3mf
cad/Backplat500stock.dxf
cad/Backplate.dxf
cad/Bracket.3mf
cad/Duct_volcano.3mf
cad/Panel_base_BRS-500.dxf
cad/RingUnifiedv2.step
cad/geo8.3mf
cad/m1-300-plate.step
cad/m1-400-plate.step
cad/m1-500-plate.step
cad/octogon.stl
cad/panel_base_BRS-300.dxf
cad/panel_base_BRS-400.dxf
cad/shroudbrs.stl
cad/xy_idler_v1.2_W.step
stl/m1-plates/400/M1/Rear R.stl
stl/m1-plates/400/M1/Top L.stl
stl/m1-plates/400/M1/Top R.stl
stl/m1-plates/400/M1/rear L.stl

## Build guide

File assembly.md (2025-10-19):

# BRS-Engineering  
## Assembly manuals

In this section you will find manuals for all upgrades. 

Printer Component|Status|View|Manual EN|Manual FR|Video|Troubleshooting guide EN
-----------------|------|-----------------------------------| :----: |  :---------------: | :---------------: | :---------------:
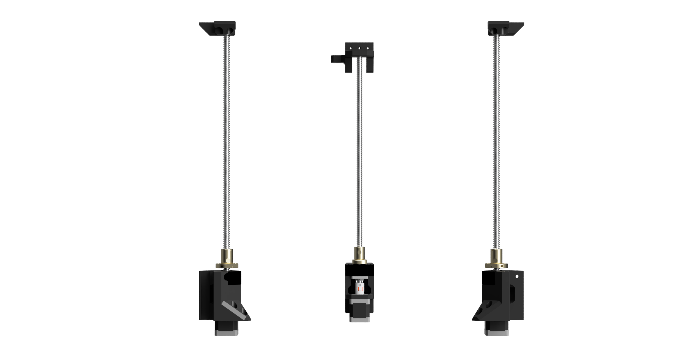
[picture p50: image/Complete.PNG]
Z system 1.x|Active|<br> **Z-Upgrade 1** Ballscrew system VCORE 3.0/3.1|[Download](/manuals/manualEN.pdf)|/||[Download](/manuals/TroubleshootingZ.pdf)  
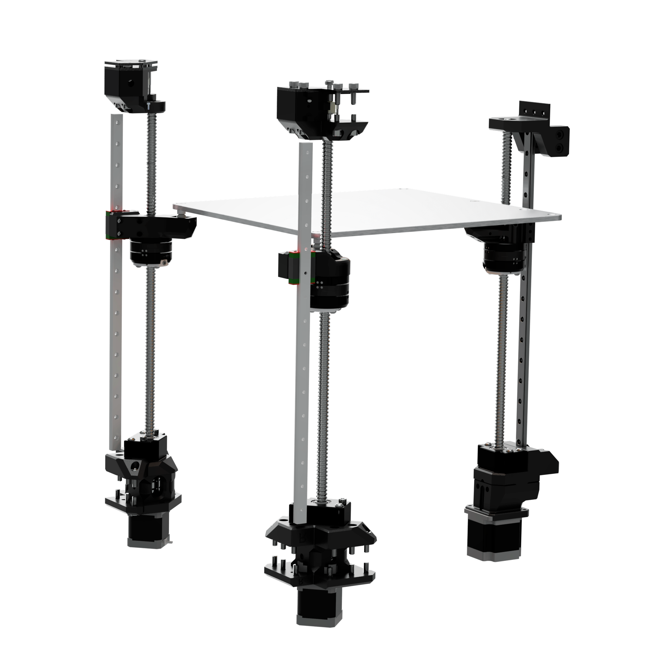
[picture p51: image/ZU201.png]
Z system 2.x|Active|<br> **Z-Upgrade 2** Ballscrew system VCORE 3.0/3.1|[Download](/manuals/Z-upgrade-28DE-manual.pdf)|/||[Download](/manuals/TroubleshootingZ.pdf)
Z system 2.8DE|Active|<br> **Z-Upgrade 2.8DE** Ballscrew system VCORE 3.0/3.1|[Download](/manuals/Z-upgrade-28DE-manual.pdf)|/||[Download](/manuals/TroubleshootingZ.pdf)
Z system 3.0|Active|<br> **Z-Upgrade 3.0 Ballscrew system VCORE 4|[Download](/manuals/Z-Upgrade-3.0-Manual-1.0.pdf)|/||/
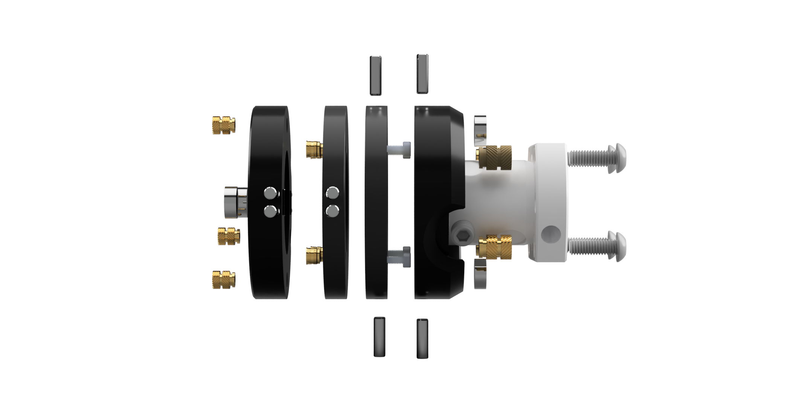
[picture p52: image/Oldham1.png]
Oldham for Vcore|Active|<br> **Oldham** for 1204 Ballscrew system|[Download](/manuals/Oldham-Manual.pdf)|/|/|
Oldham for Raise3D|BETA|<br> **Raise3D Oldham** for 2005 Ballscrew system|[Download](/manuals/Raise-Oldham-Manual.pdf)|/|/|
BRS-AWD-Drives 2.1 |Active|<br> **BRS-AWD-Drives 2.1**|[Manual](manuals/BRS_AWD_Drive_2.0_VC4.pdf)|/|/
BRS-AWD-Drives 1.35|Active|<br> **BRS-AWD-Drives**|[Manual](manuals/BRS-AWD-Drive-V135a.pdf)|/|/
PMB v1.2-2.0|Active|<br> Heavy duty Precision motor block|[Download](/manuals/Manual-PMB.pdf)|/||[Download](/manuals/Troubleshooting-M1-M2.pdf) 
L3VER M1 A1.1/A1.2-Refresh|Active|<br> Heavy duty Tensionner for BRS open frame design, and Tensionnerless Head like Flathead V3 and VZbot head|[Download](/manuals/Lever-m1-manual.pdf)|/| [VIDEO](https://drive.google.com/file/d/1_cTKRS3Ra1BuopSvnplw1cQjTDOn0Drg/view?usp=sharing) | [Download](/manuals/Troubleshooting-M1-M2.pdf) 
L3VER M2 A1.1|Active|<br> Heavy duty integrated Tensionner, and Tensionnerless Head like Flathead V3 and VZbot head|[Download](/manuals/Lever-m2-manual.pdf)|/||[Download](/manuals/Troubleshooting-M1-M2.pdf)
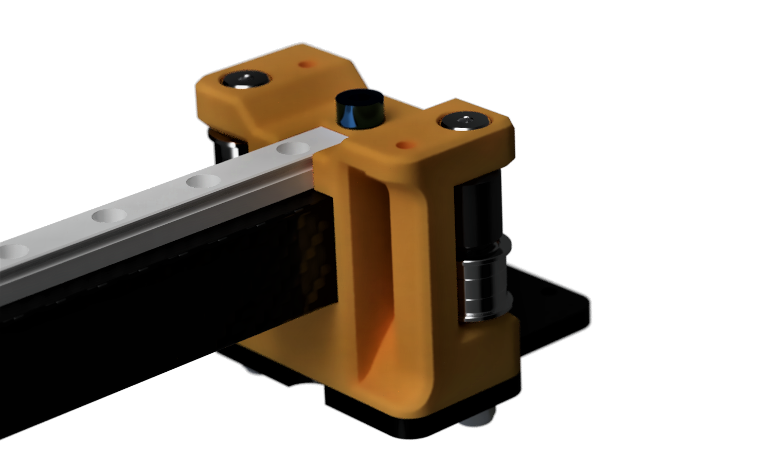
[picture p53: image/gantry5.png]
Ultralight Gantry|Active|<br> **Ultralight gantry** |[Download](/manuals/Ultralight-Gantry-Manual.pdf)|/|| 
Flathead V2|Active|<br> **FlatheadV2**|[Download](/manuals/manualEN.pdf)|/|/
CF80 Filtration unit|Active|<br> **CF80 Filtration unit**|[Download](/manuals/CF80-Manual.pdf)|/|/
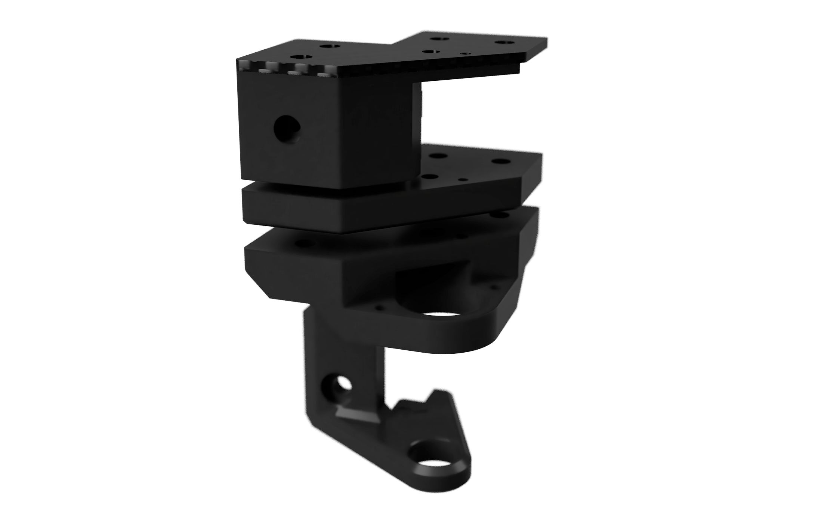
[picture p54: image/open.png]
Open front blocks V2|Active|<br> **Open front V2**|[Download](/manuals/open-Manual.pdf)|/|/
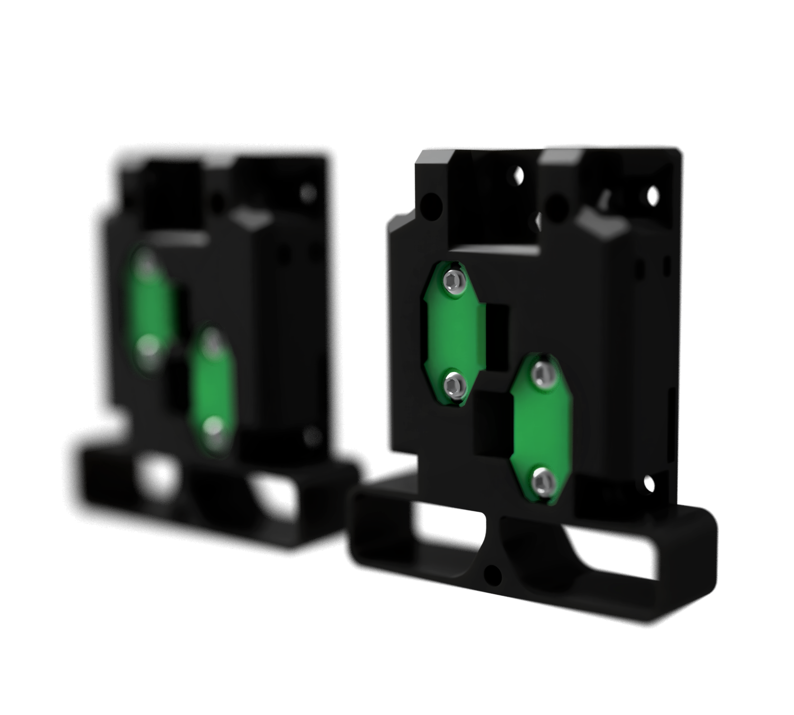
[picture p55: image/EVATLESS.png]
EVA3-Tensionnerless|Active|<br> **EVA3-Tensionnerless**|[Download](/manuals/EVA3-Tensionnerless-Instructions.pdf)|/|/

## [Back to Main Page](/README.md)

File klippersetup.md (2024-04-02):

Disclaimer: This page is still under construction, I'm implementing content I will found legit to make a Pure straightforward Klipper/Mainsail setup, this is exactly the way I'm making my machines. It is not a complete guide, it is here to guide you for the main setup. You must build the printer cfg according the pinout layout and your specific hardware. you must be sure that the cables are correctly set to be fonctionnal too, this guid is not a wiring guide.

# Installation

These instructions assume the software will run on a Raspberry Pi computer. It is recommended that a Raspberry Pi 2 (or later) be used as the host machine. RPi 4 and 5 are recommended to achieve good performance. CM4 modules with EMMC >=16Go is a good option for specific MCU boards too.
This page is dedicated to a full Klipper Mainsail installation from the start, as a pure instalation. A KIAUH installation is possible too,
I'm making this page as I'm making my own machines

# Prepping an OS image

Start by downloading Rasberry Pi image ([here](https://www.raspberrypi.com/software/)), Then follow the steps



By clicking we go to Mainsail OS, a package with Klipper and Mainsail already pre-installed. We can follow this route:





"Enable SSH" and then click "Save", there are other functions that can be set in this interface, please modify them according to your needs.

Since we have selected the most recent version of Mainsail OS, we can select the SD card and configure the wifi. For this we have these options:



It is important to choose a quality and fast micro SD card, since a slow card can hinder the performance of the device.



Wait for the process to complete.

# Building and flashing the micro-controller

Use PUTTY to connect you controller, I use Advanced IP scanner to check the IP adress



To compile the micro-controller code, start by running these commands on the Raspberry Pi:

```
cd ~/klipper/
make menuconfig
```
Follow you motherboard manual to get the correct settings to apply


exemple

Once done you can quit

The comments at the top of the printer configuration file should describe the settings that need to be set during "make menuconfig". Open the file in a web browser or text editor and look for these instructions near the top of the file. Once the appropriate "menuconfig" settings have been configured, press "Q" to exit, and then "Y" to save. Then run:
```
make
```
After the make command is executed, the klipper.bin firmware we need will be generated in the device's home/pi/klipper/out folder. You can download it directly to your computer with WINSCP
According to you board model (here BTT), Rename `klipper.bin` to "firmware.bin", copy it to the root directory of the SD card, insert the SD card into the MCU SD card slot, press the reset button or power on again, and the firmware will be automatically updated.
After the update is complete, the "firmware.bin" in the SD card will be renamed to "FIRMWARE.CUR".

In PUTTY, enter
```
ls /dev/serial/by-id/*
```
It should report something similar to the following:



It's common for each printer to have its own unique serial port name. This unique name will be used when flashing the micro-controller. It's possible there may be multiple lines in the above output - if so, choose the line corresponding to the micro-controller.
Copy this ID for later

>**If nothing is shown, please check the cable connection between the PI and the main MCU board. Please check the compile settings are correct (sometime STM32 chips can be mistaken), please always confirm the "firmware.bin" is transformed to "firmware.cur" to confirm a successful flash.**

# First Connection

You can now Access the WEBUI of the machine via any Browser. The machine will report ERRORS, that is normal, we dont have any cfg installed.
We will make the updates to be as fresh as we can.
Check the Config Tab and make the according update if available. I suggest before doing anything, UPDATE ALL and/or install all the things you need (Telegram bot etc)


# UPDATE and disclaimer

AT THIS POINT, I STRONGLY SUGGEST TO NEVER DO ANY UPDATE TO KEEP A WORKING MACHINE FONCTIONNAL
Update can wreck you system and take time to solve and remake. If a machine works fine, DON'T DO ANY UPDATES
Update are relevent if a major add on or support is added for new hardware or new fonctionnality, please consider the balance between benefits and risks of such an thing.

# Host MCU (RPi)

In many case scenarios, the RPi will be used as a secondary MCU (GPIO pins, etc). It is a good idea to flash it as a secondary MCU if you want to ad Fans, Servo, custom modules, relays...

Open a PUTTY instance to install the RC script:
```
cd ~/klipper/
sudo cp ./scripts/klipper-mcu.service /etc/systemd/system/
sudo systemctl enable klipper-mcu.service
```
Then we build the MCU code
```
cd ~/klipper/
make menuconfig
```



select "linux process", quit the menu
Then we flash it
```
sudo service klipper stop
make flash
sudo service klipper start
```
If klippy.log reports a "Permission denied" error when attempting to connect to /tmp/klipper_host_mcu then you need to add your user to the tty group. The following command will add the "pi" user to the tty group:
```
sudo usermod -a -G tty pi
```
Optionnally you can enable SPI and GPIOCHIP

Make sure the Linux SPI driver is enabled by running
```
sudo raspi-config 
```
and enabling SPI under the "Interfacing options" menu.

For GPIO tools:
```
sudo apt-get install gpiod
```
```
gpiodetect
```
```
gpioinfo
```
To call a PIN as a fonction, by exemple a CPAP PWM signal modulation, you need to adress the FAN pin as



Meaning you will use the pin on the GPIOpin 20 here. To check GPIO pin availability, run the upper commands (gpiodetect, gpioinfo)

# Printer.CFG

The Printer.cfg is the config file containing all the settings linked to the machine
You must build you own depending you MCU PIN layout, Machine architecture, and custom hardware, [Here a file used in the last VUCLAIN 600 v1.3](printer.cfg)
In this file must be mentionned the ID of the MCU(s) identified previously via the command

I personnaly don't like to make too much INCLUDES, calling different CFGs. RatOS by exemple use an insanely high count of that, making the adjustement and the cfg readings quite difficult and hard to remember in my opinion. As RatOS is meant for versatility it is understandable, but here we are making a quite straightforward config, sometime keeping it simple is the way. 
I prefer using a complete printer.cfg, and if I need to, includes some specific auxilliary CFGs, like a macros.cfg (only for MACROS), a Toolhead.cfg (for CanBus toolheads) and eventually some exotic hardware like Euclid probes settings

```
ls /dev/serial/by-id/*
```
Like this



To add the RPi MCU previously prepare, you must include 



# BELT TENSION RESONNANCE
```
TEST_RESONANCES AXIS=1,1 OUTPUT=raw_data
```
```
TEST_RESONANCES AXIS=1,-1 OUTPUT=raw_data
```

Then run this line in PUTTY the instance:
```
~/klipper/scripts/graph_accelerometer.py -c /tmp/raw_data_axis*.csv -o /tmp/resonances.png
```

# INPUT SHAPER

Make sure your ADXL based module is configured correctly
The way this one is attached to the toolhead will matter a lot, a loosy fixation a placment will result a bad shaping
The best place is in the nozzle (the BTT ADXL V2 is the best option IMO). You will use it only on this occasion and then removed it after use

Keep in mind that getting a not perfect shaper is not the end of the world, it is here to counterbalance thos issues.
Only the print result count at the end of the day

First check the acceleromete fonction nwith ```ACCELEROMETER_QUERY``` in the printer CLI
you should get something like this
```
Recv: // adxl345 values (x, y, z): 470.719200, 941.438400, 9728.196800
```
Then run 
```
TEST_RESONANCES AXIS=X
```
```
TEST_RESONANCES AXIS=Y
```

and finally those lines in the  Putty instance
```
~/klipper/scripts/calibrate_shaper.py /tmp/resonances_x_*.csv -o /tmp/shaper_calibrate_x.png
```
```
~/klipper/scripts/calibrate_shaper.py /tmp/resonances_y_*.csv -o /tmp/shaper_calibrate_y.png
```

you can now grab the PNGs of the shaper and make you analysis

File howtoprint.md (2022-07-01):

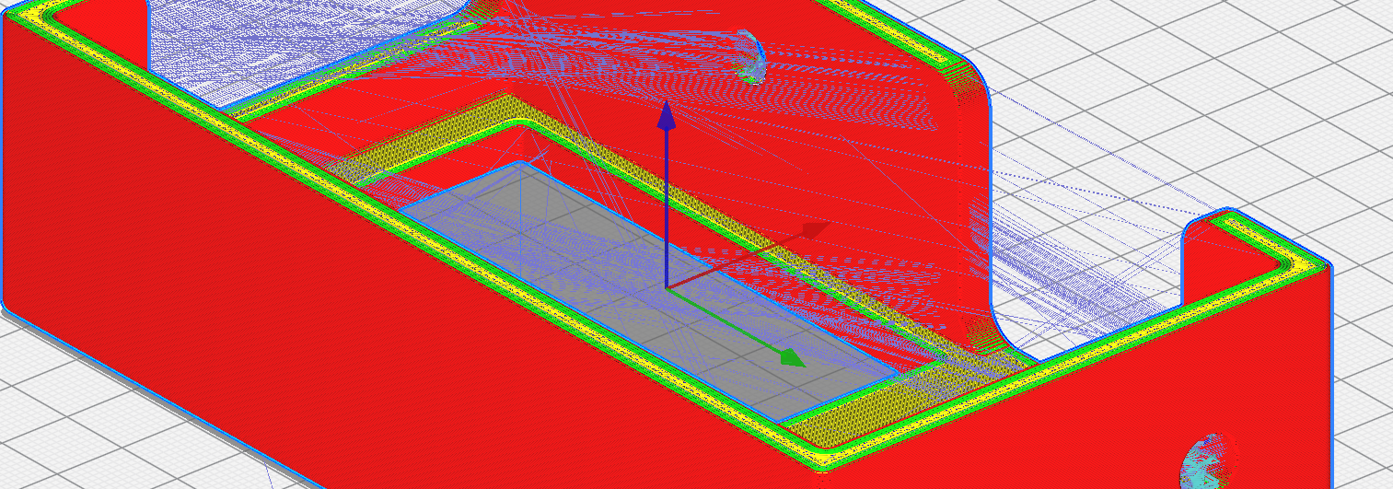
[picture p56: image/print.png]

# How to print the BRS parts?

## 1. Which material?
Pretty much any common 3D printing material can be used.

I design it to print with PACF material such as Fibelogy PA12CF15 or Esun ePAHT

PA12 from Fiberlogy is very easy when the profile is fine tuned
ePAHT is a pain to get ok, spool must be dryed 12h @80°C, and parts annealed at 80-110°C for 3-6h, failure rate is higher that PA12CF and the pros to use ePAHT are non-existant in the context of the Vcore parts

I am currently running PA12CF15 for my own machine

## 2. Placing your parts in the slicer.
All STL files are already properly oriented for optimal print results and optimal layer orientation.  

## 3. Slicer Settings
In this section I will assume that you have some experience with 3D printing and that your printer is calibrated.
PACF dont bridge well, Supports and supports intefaces are needed, Make samples before going big, suppports could be unremovable otherwise

____________________________________________________________________________________  

### QUALITY

Section|Setting|Recommended Value|Comment
-------|-------|-----------------|-------
Quality|Layer Height|Between 0.16 and 0.22| No structural or precision gain by going lower than 0.16. 
Quality|Line Width|0.40 (for 0.4mm nozzle)| - 

______________________________________________________________________________  

### SHELL

Section|Setting|Recommended Value|Comment
-------|-------|-----------------|-------
Shell|Wall Line Count|3 to 4|-
Shell|Top/Bottom thickness|1.2mm|This means between 9 and 5 top and bottom layers, depending on your layer height. I use a 0.26mm first and last Layer width to get better finish 

### INFILL

Section|Setting|Recommended Value|Comment 
-------|-------|-----------------|-------
Infill|Infill Density|18-25%|Going higher will not add significant strength.
Infill|Infill Pattern|Gyroid|The advantages of gyroid: high shear strength, and low weight (so less filament needed) and less cross pattern, which reduce risks of shifting.

### SPEED

This parameter is free for you to decide

-For classic Ender type printer, 60-70mm/s is a nice spot. 
-For higher end machines (Vcore) I can crank to 200mm/s without any loss of quality and strenght

## Flathead v2 parts settings

Section|Setting|Recommended Value|Comment|Orientation
-------|-------|-----------------|-------|-------
Shell|Wall Line Count|5 to 6|-
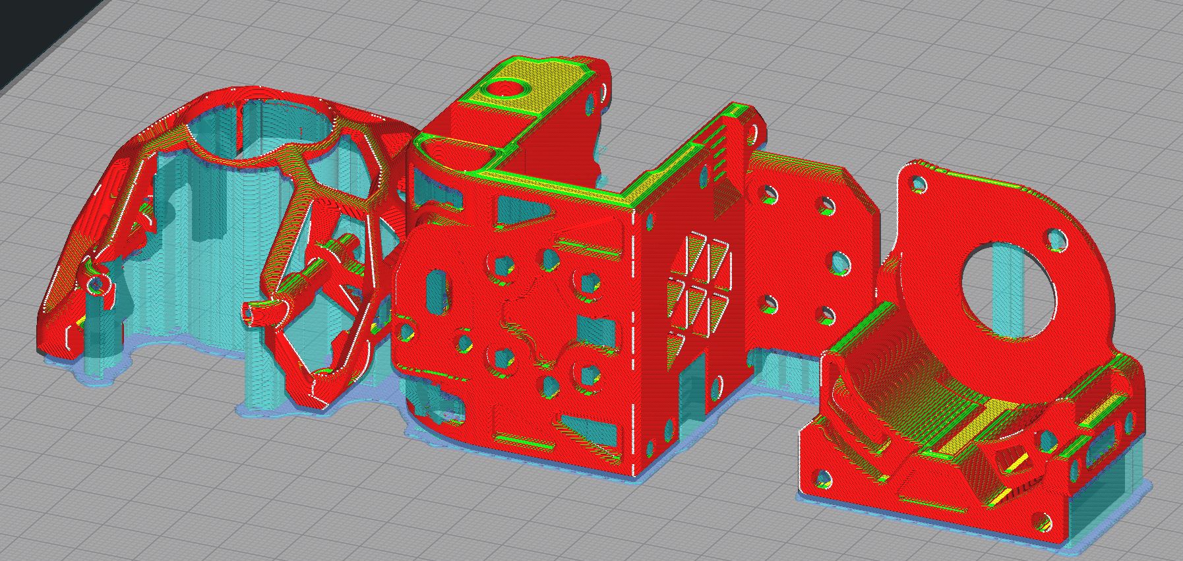
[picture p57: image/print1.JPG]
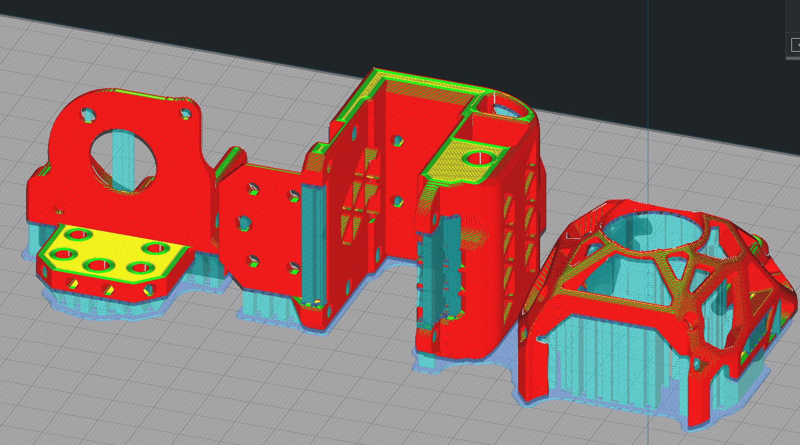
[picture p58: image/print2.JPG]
Shell|Top/Bottom thickness|1.2mm|This means between 9 and 5 top and bottom layers, depending on your layer height. I use a 0.26mm first and last Layer width to get better finish, Light supports needed |IMPORTANT  

## Z-Upgrade Rear part

Section|Setting|Recommended Value|Comment|Orientation
-------|-------|-----------------|-------|-------
Shell|Wall Line Count|4 to 6|-
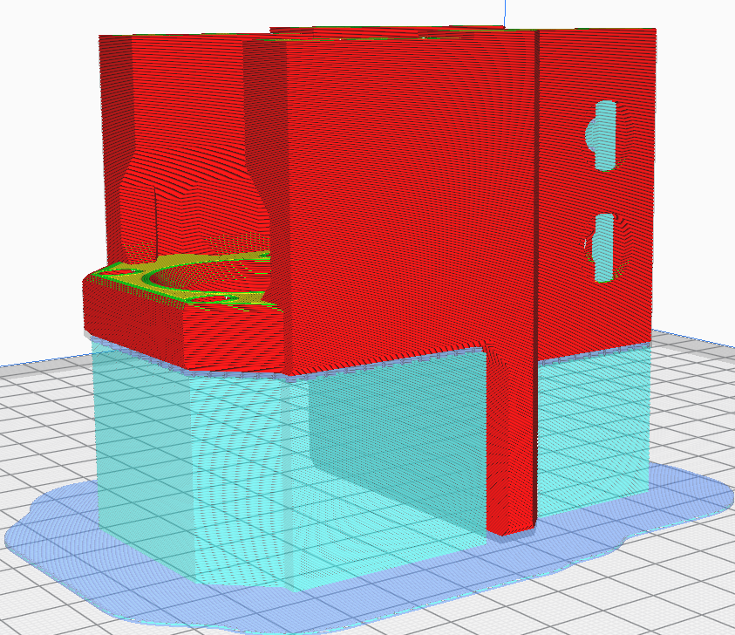
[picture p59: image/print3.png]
Shell|Top/Bottom thickness|1.2mm|This means between 9 and 5 top and bottom layers, depending on your layer height. I use a 0.26mm first and last Layer width to get better finish, supports needed with an interface to ensure quality surface? In termls of support it is the worse part to print but it is very stable for the final parts strengh |IMPORTANT 

[Back to Main Page](/README.md)

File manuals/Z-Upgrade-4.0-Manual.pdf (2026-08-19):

### Z-Upgrade 4.0 for VCORE 4.0/4.1

BRS-Engineering

Page 1 sur 30

# Z-Upgrade 4.0 manual

### Evolutions

Indice | Date | Description de l’évolution | Auteur
0.0 | 30/01/2026 | Création | FBR
0.1 | 25/03/2026 | 1204 implementation | FBR
0.2 | 28/03/2026 | 1204 FK10 simplification | FBR
0.3 | 25/04/2026 | Locknut deletion + Troubleshooting implementation | FBR
0.4 | 19/08/2026 | Heavy duty (HD) addition | FBR

### Z-Upgrade 4.0 for VCORE 4.0/4.1

Page 2 sur 30

## 1 Introduction

First, a big thanks if you have purchased the kit from my store, it helps me to continue development and fuel my passion

If you are a Hobbyist and make this mod on your side as DIY, welcome to the project!

## 2 Parts preparation

Those steps don’t concern you if you bought your kit at BRS store, as I deliver it pre-assembled

# Mainparts commons

Place 18x M3 inserts over the main blocks, All 3 blocs have the same layout, 6 on each.

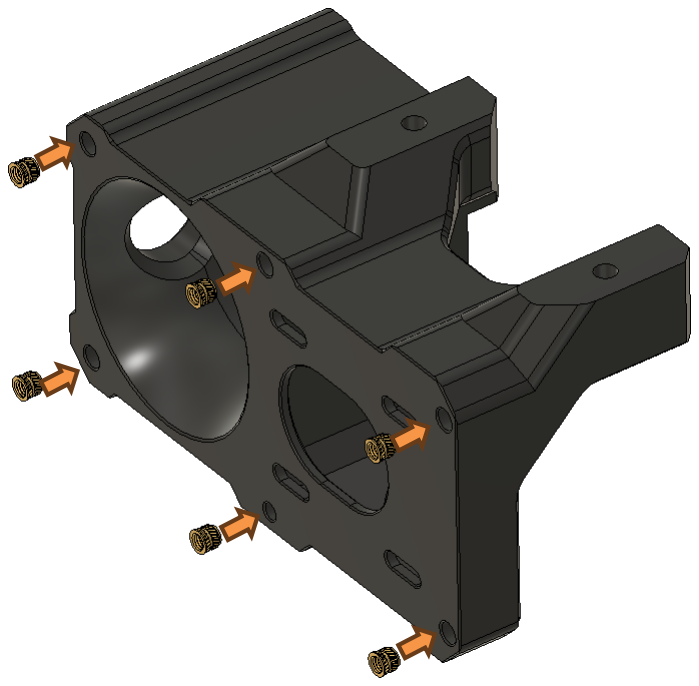
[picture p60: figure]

FOR LEGACY / 1204 VERSION:

Insert the M4x10mm insert in the top of the part

A long M4 insert here is needed, the goal is to provide a strong bond

### Z-Upgrade 4.0 for VCORE 4.0/4.1

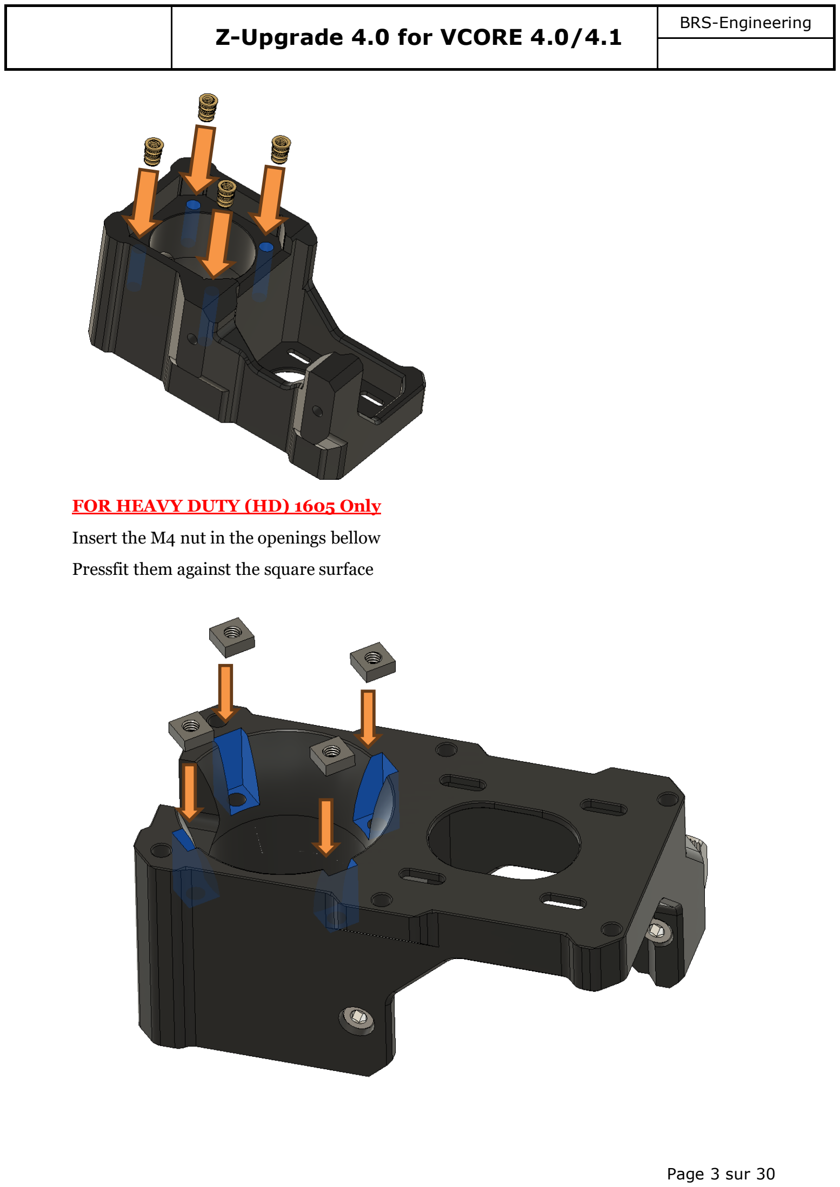
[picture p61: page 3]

Page 3 sur 30

FOR HEAVY DUTY (HD) 1605 Only

Insert the M4 nut in the openings bellow

Pressfit them against the square surface

### Z-Upgrade 4.0 for VCORE 4.0/4.1

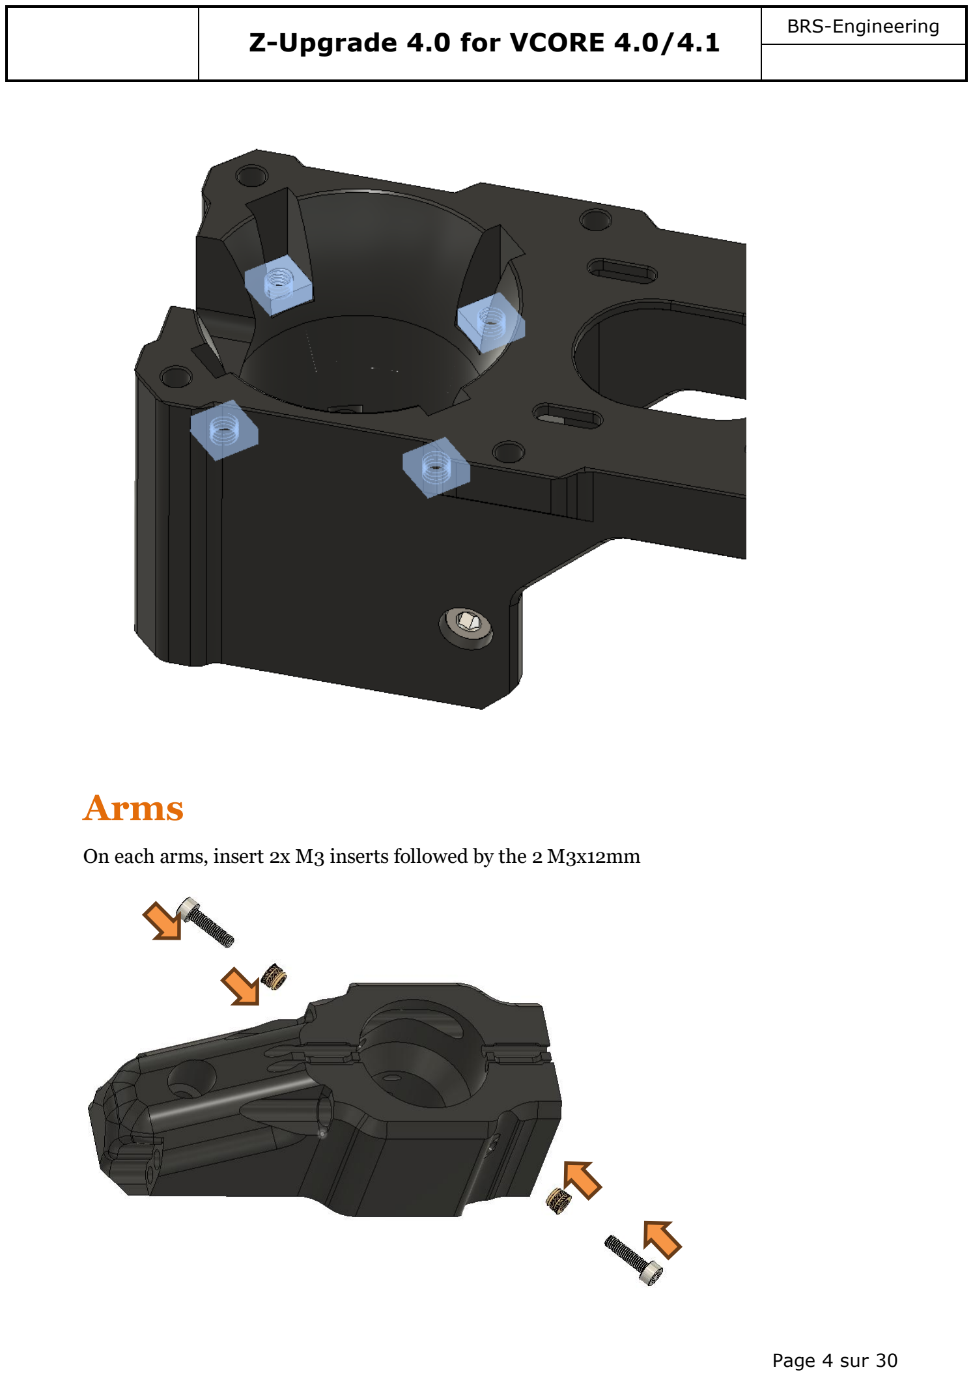
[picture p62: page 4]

Page 4 sur 30

# Arms

On each arms, insert 2x M3 inserts followed by the 2 M3x12mm

### Z-Upgrade 4.0 for VCORE 4.0/4.1

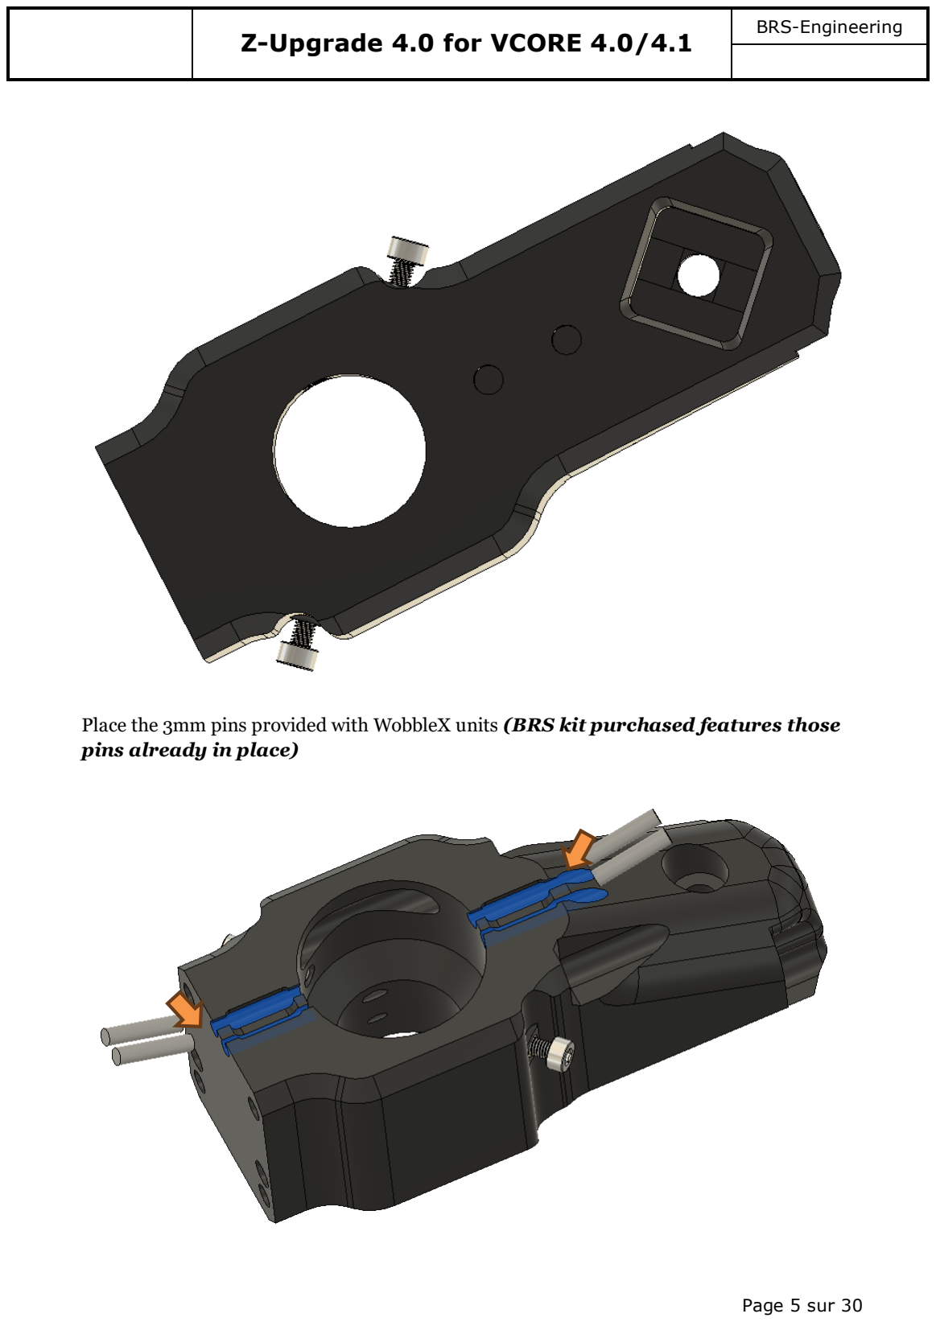
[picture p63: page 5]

Page 5 sur 30

Place the 3mm pins provided with WobbleX units (BRS kit purchased features those pins already in place)

### Z-Upgrade 4.0 for VCORE 4.0/4.1

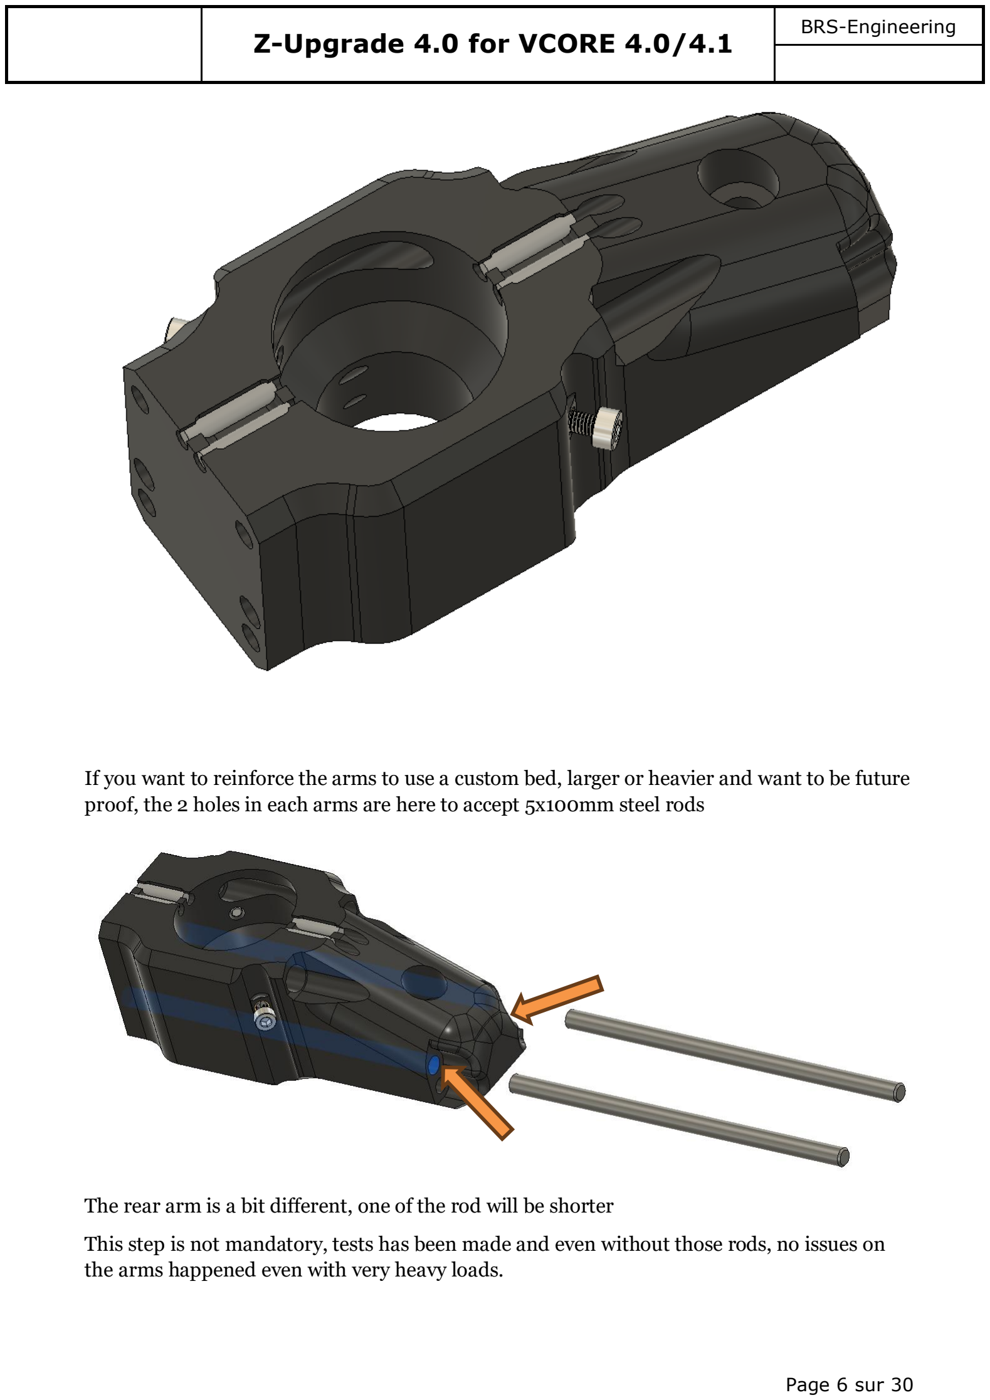
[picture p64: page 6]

Page 6 sur 30

If you want to reinforce the arms to use a custom bed, larger or heavier and want to be future proof, the 2 holes in each arms are here to accept 5x100mm steel rods

The rear arm is a bit different, one of the rod will be shorter

This step is not mandatory, tests has been made and even without those rods, no issues on the arms happened even with very heavy loads.

### Z-Upgrade 4.0 for VCORE 4.0/4.1

Page 7 sur 30

At this point you can install the wipers, and the top retainer, and the belt grabber and wire organizer following the Vcore Rat rig manual since nothing changed

## 3 Tensionner + Bottom cage

Note: The HD version and legacy version are using the same design but with different thickness here! Same logic anyway

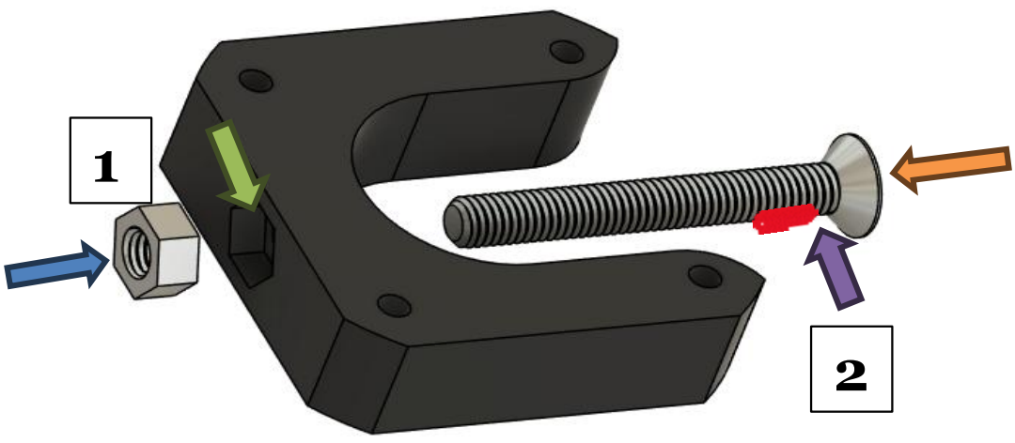
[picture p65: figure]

Apply glue in the nut part location. Install a M5 nut or a Nyloc M5, then let it dry 5 min. Apply glue or threadlocker on the first 6mm of the screw. Install the screw fully! Let it dry 10min

Place in inside the bottom cage

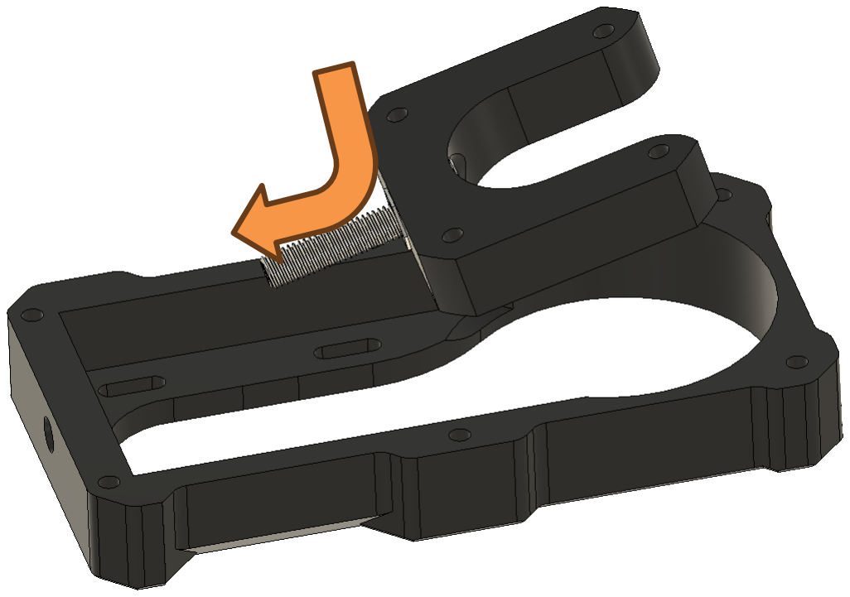
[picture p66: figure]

### Z-Upgrade 4.0 for VCORE 4.0/4.1

Page 8 sur 30

Add the washer and the knob, but don’t tight it yet

Preinstall the screws for later

### Z-Upgrade 4.0 for VCORE 4.0/4.1

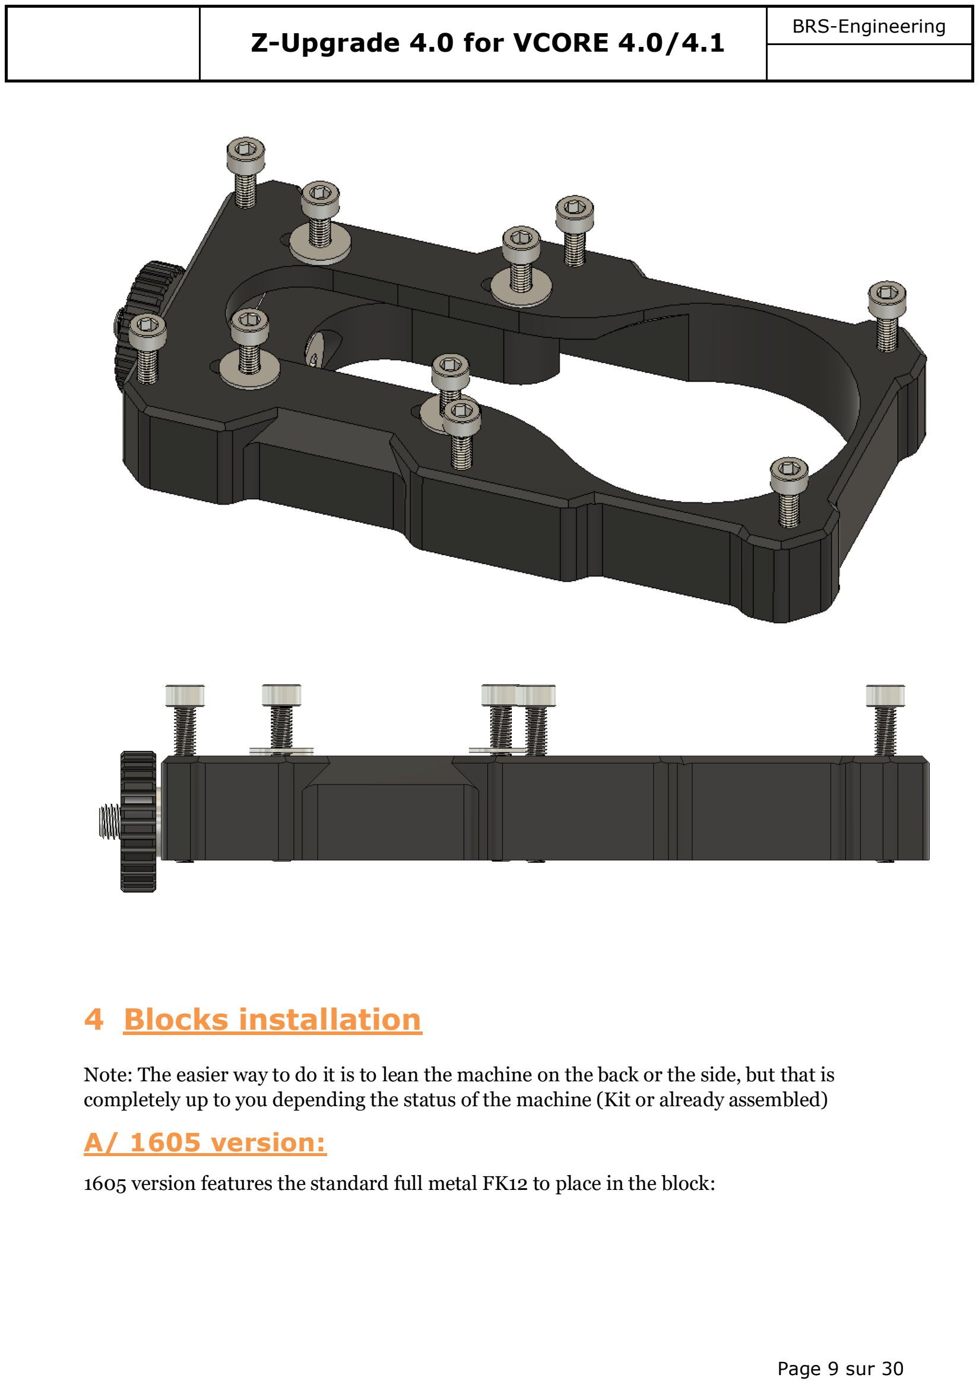
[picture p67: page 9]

Page 9 sur 30

## 4 Blocks installation

Note: The easier way to do it is to lean the machine on the back or the side, but that is completely up to you depending the status of the machine (Kit or already assembled)

### A/ 1605 version:

1605 version features the standard full metal FK12 to place in the block:

### Z-Upgrade 4.0 for VCORE 4.0/4.1

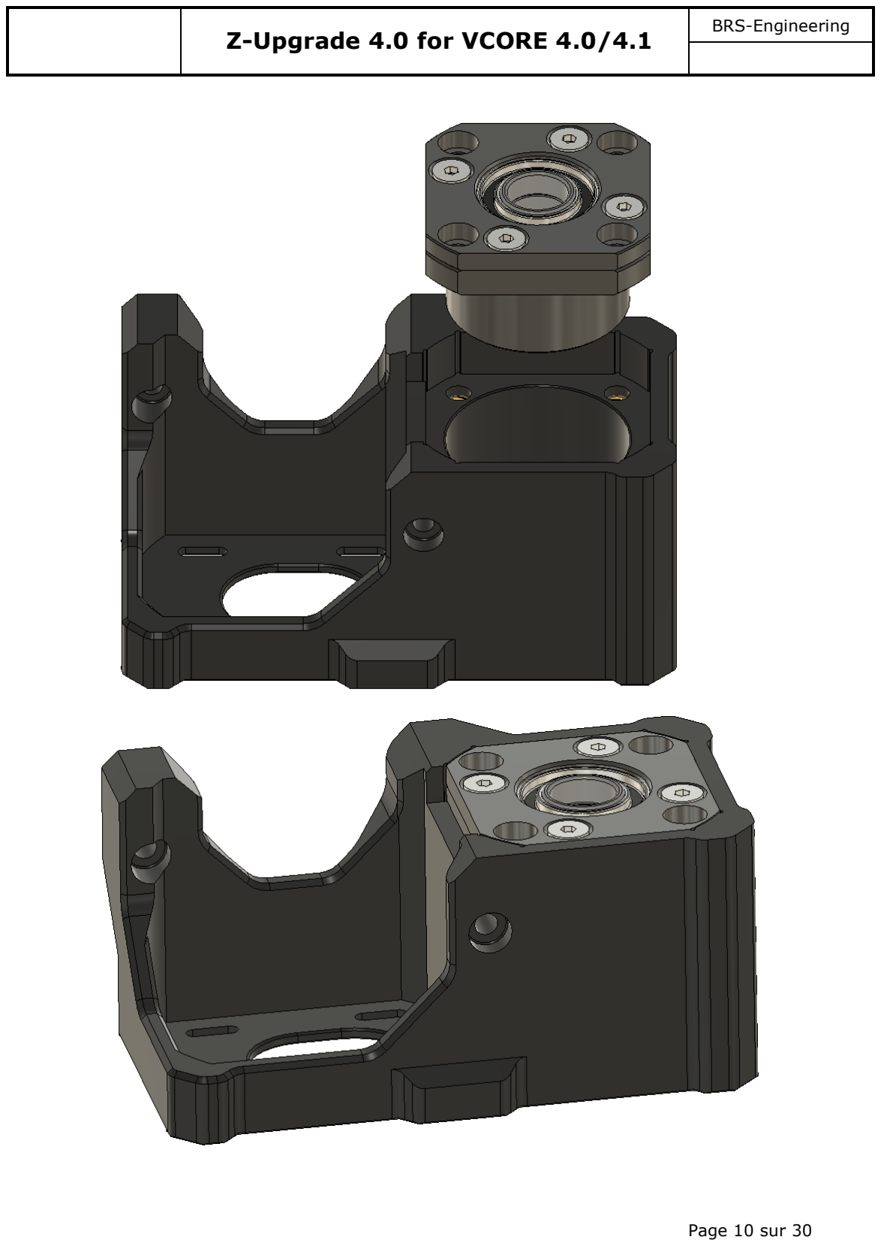
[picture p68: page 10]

Page 10 sur 30

### Z-Upgrade 4.0 for VCORE 4.0/4.1

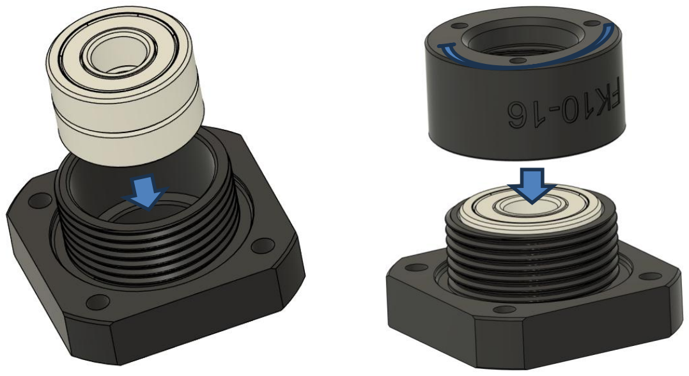
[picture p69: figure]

Page 11 sur 30

### B/ 1204 version:

Here wee need to use a small variant; as hole would not self align, you need to make the FK10 replacement with the printed version, featuring correct holes alignement

The FK10 custom is made with 2 parts, which are screwing on themselves to completely secure the whole as a block

This way the bearing are completely constrained, and not hardware is needed

Pressfit the 2 6000zz (or 2RS) bearing (For DIYer, angular contact or standard can be used)

Don’t install the spaced under, as the locknut afterwards, since the last revision we don’t use them anymore

### Z-Upgrade 4.0 for VCORE 4.0/4.1

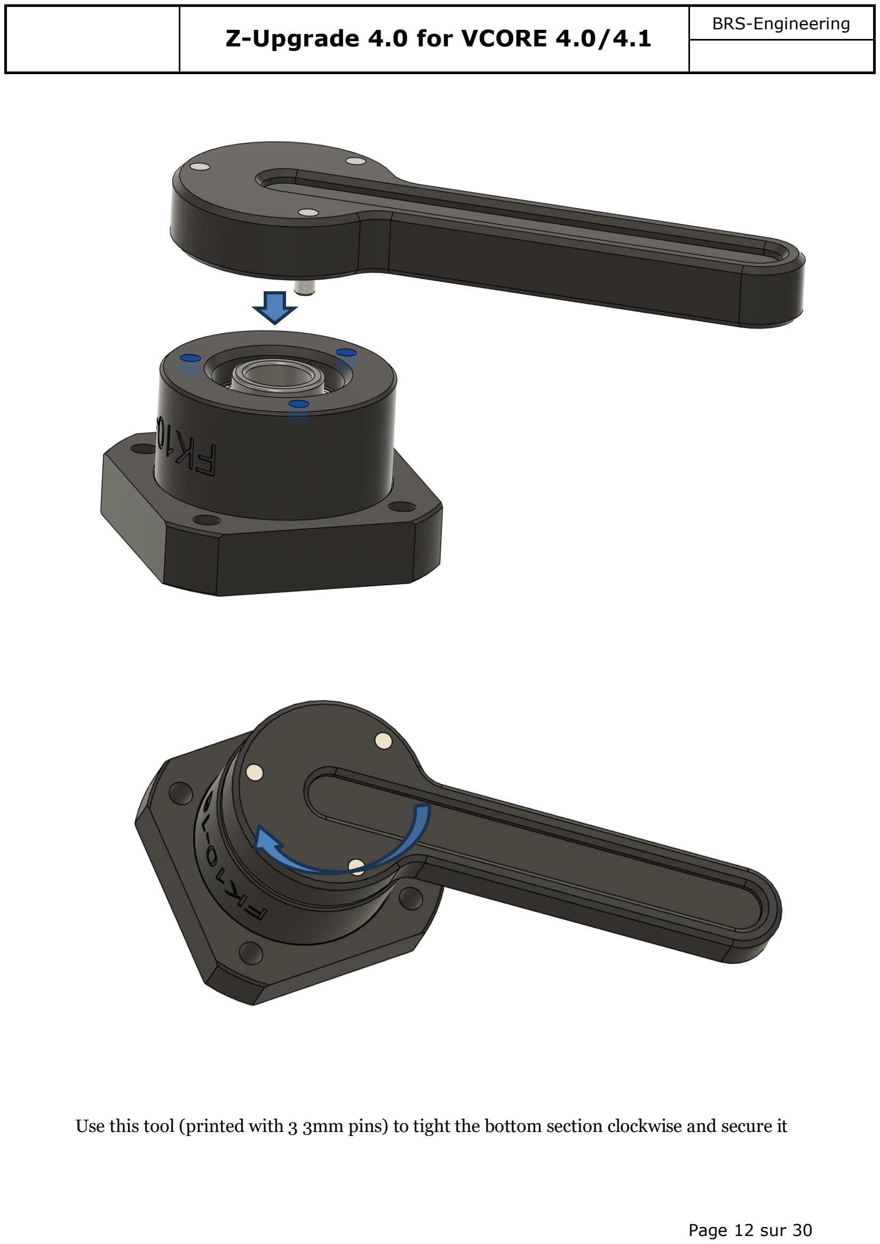
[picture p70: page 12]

Page 12 sur 30

Use this tool (printed with 3 3mm pins) to tight the bottom section clockwise and secure it

### Z-Upgrade 4.0 for VCORE 4.0/4.1

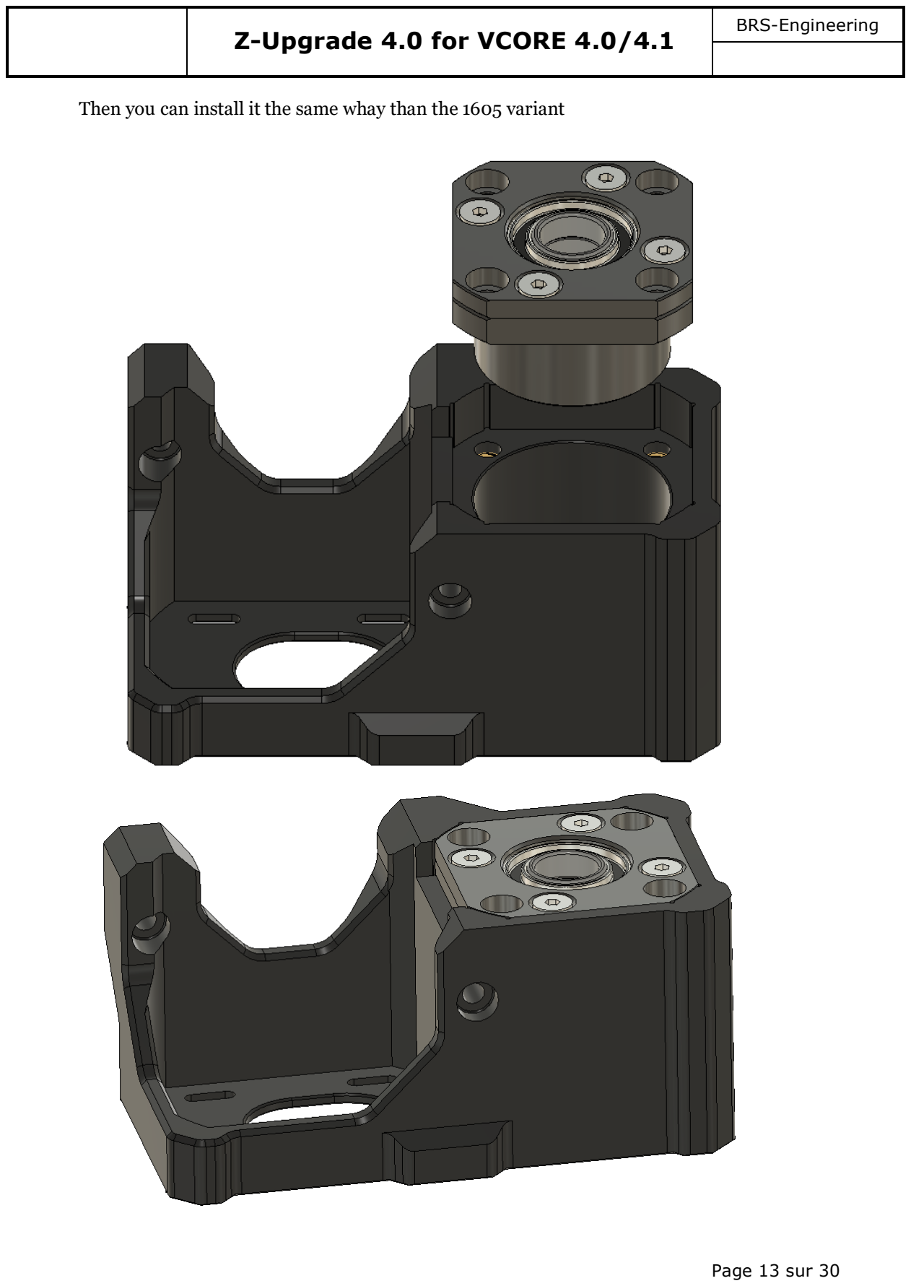
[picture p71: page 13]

Page 13 sur 30

Then you can install it the same whay than the 1605 variant

### Z-Upgrade 4.0 for VCORE 4.0/4.1

Page 14 sur 30

Install the NEMA17 (remember this model accept up to a 48mm motor, not more), and attach the 20T pulley (0.5mm from the motor base).

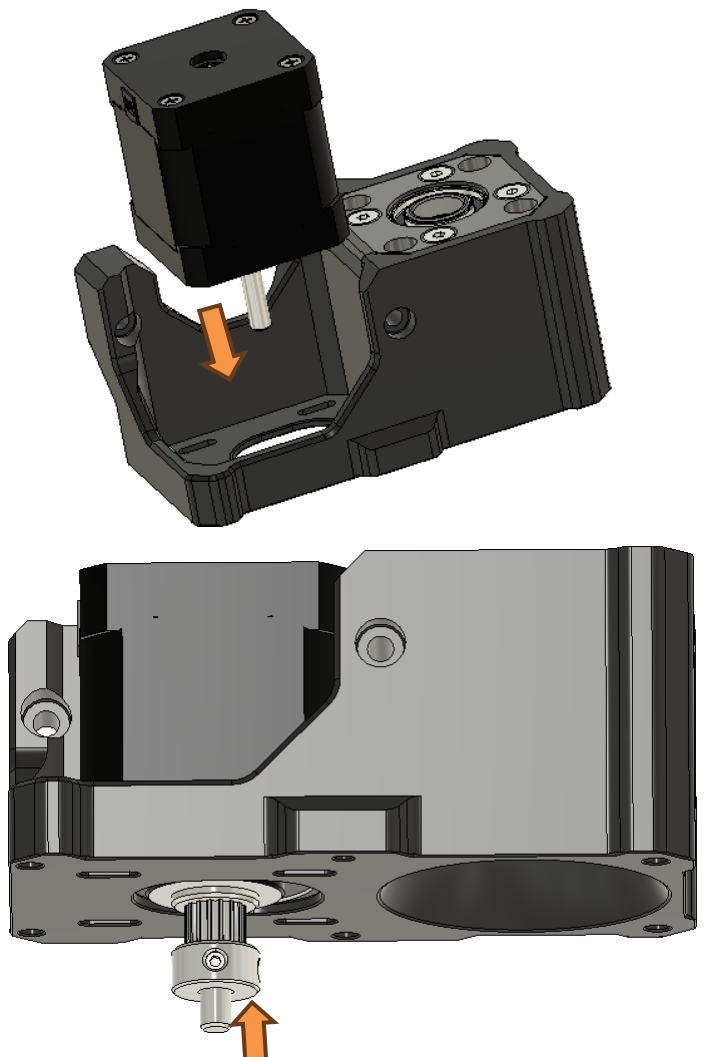
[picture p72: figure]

Install the M4 screws with the hammer nut (loosed) to prepare the anchoring

M4x60mm and M4x20mm for ech front arm, M4x20 and M4x90 for the rear block

### Z-Upgrade 4.0 for VCORE 4.0/4.1

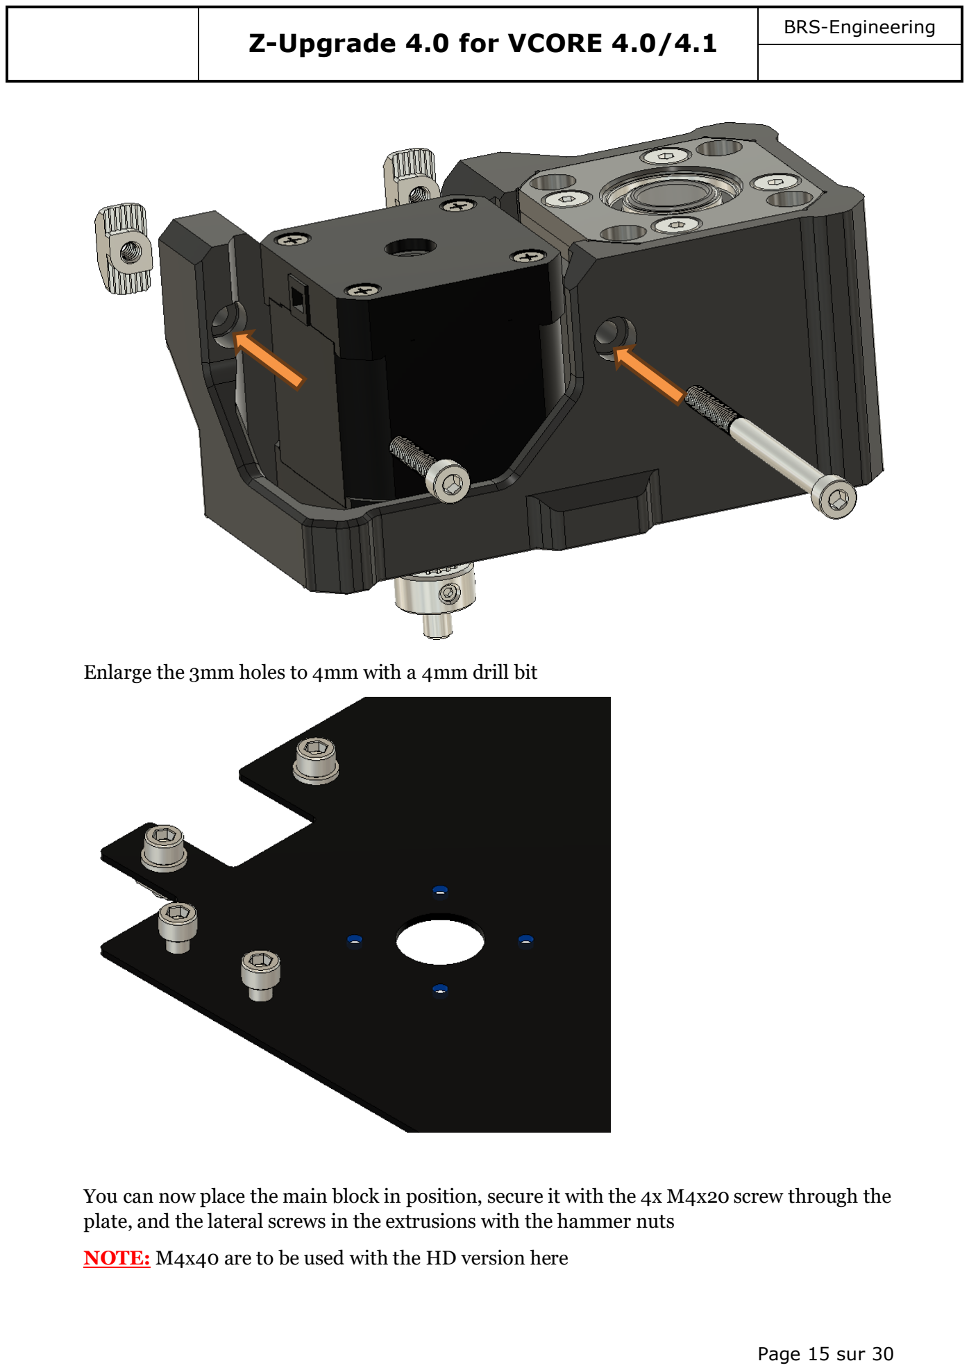
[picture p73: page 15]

Page 15 sur 30

Enlarge the 3mm holes to 4mm with a 4mm drill bit

You can now place the main block in position, secure it with the 4x M4x20 screw through the plate, and the lateral screws in the extrusions with the hammer nuts

NOTE: M4x40 are to be used with the HD version here

### Z-Upgrade 4.0 for VCORE 4.0/4.1

Page 16 sur 30

Repeat this process for the 3 blocks

### Z-Upgrade 4.0 for VCORE 4.0/4.1

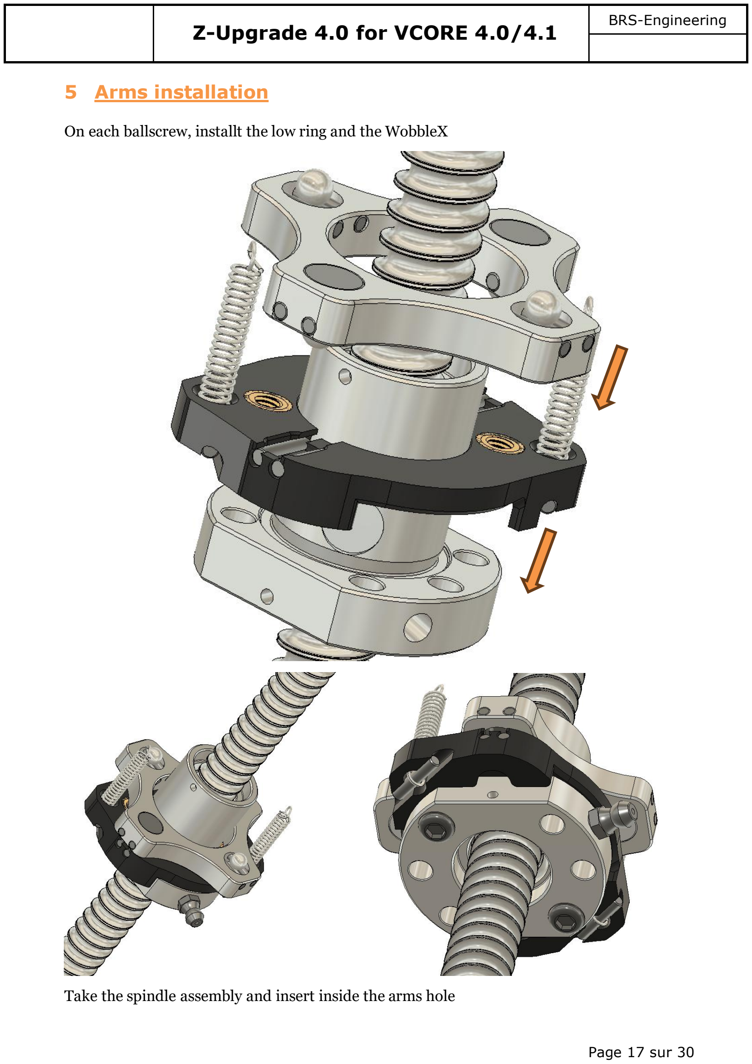
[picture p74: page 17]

Page 17 sur 30

### 5 Arms installation

On each ballscrew, installt the low ring and the WobbleX

Take the spindle assembly and insert inside the arms hole

### Z-Upgrade 4.0 for VCORE 4.0/4.1

Page 18 sur 30

Details

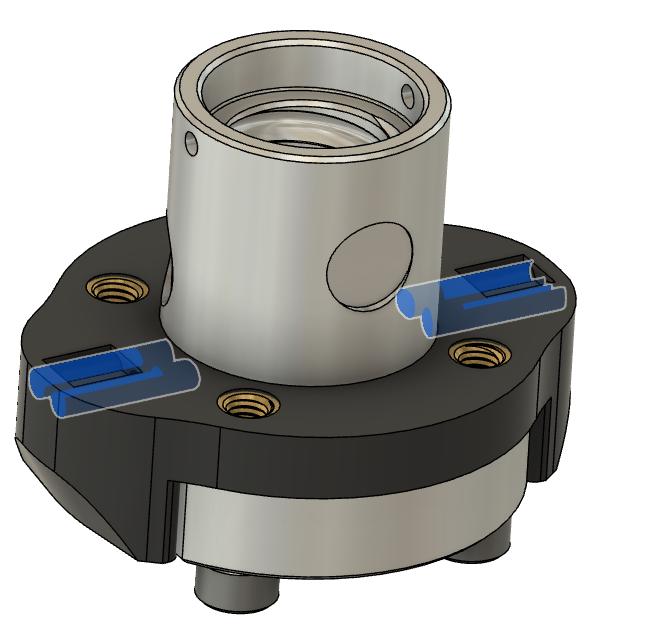
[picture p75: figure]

Pins locations

For the wobbleX (12/16), same logic: Add some M5x20 to fix the BS nut to the lower ring, add the WobbleX middle ring and install it the same way with the spindle motion seen above.

Be careful: 1204 and 1605 version got some differences:

-Discs are larger, and use a different layout, 1605 and 1204 are not compatible between each others, M5x16 are used to secure the ring, with 1204 you need the m4x16

### Z-Upgrade 4.0 for VCORE 4.0/4.1

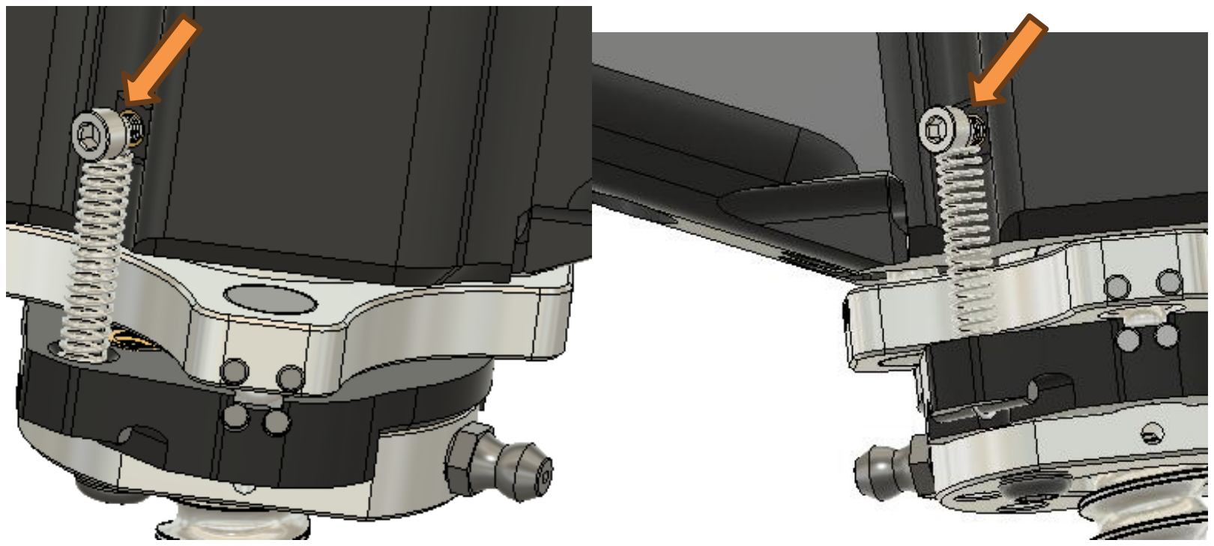
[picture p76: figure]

Page 19 sur 30

-Arms got a different hole layout and dimension as their pins position

At this point you can change the methods, as few exist to get to the same objective.

3.2D revision :

The last revision features a spring retainer to avoid lifting the full assembly and loose the ball from the WobbleX

Insert the spring in the hole, secure it with a pin

This under ring feature only 2 M5 screw new, proved to be enough in this case.

At the end of the unit assembly, use a plier to tension the spring and reach the arm mount point

### 6 Ballscrews installation

Now insert the other machined end inside the plate hole, until the ballcrew get fixed in position

### Z-Upgrade 4.0 for VCORE 4.0/4.1

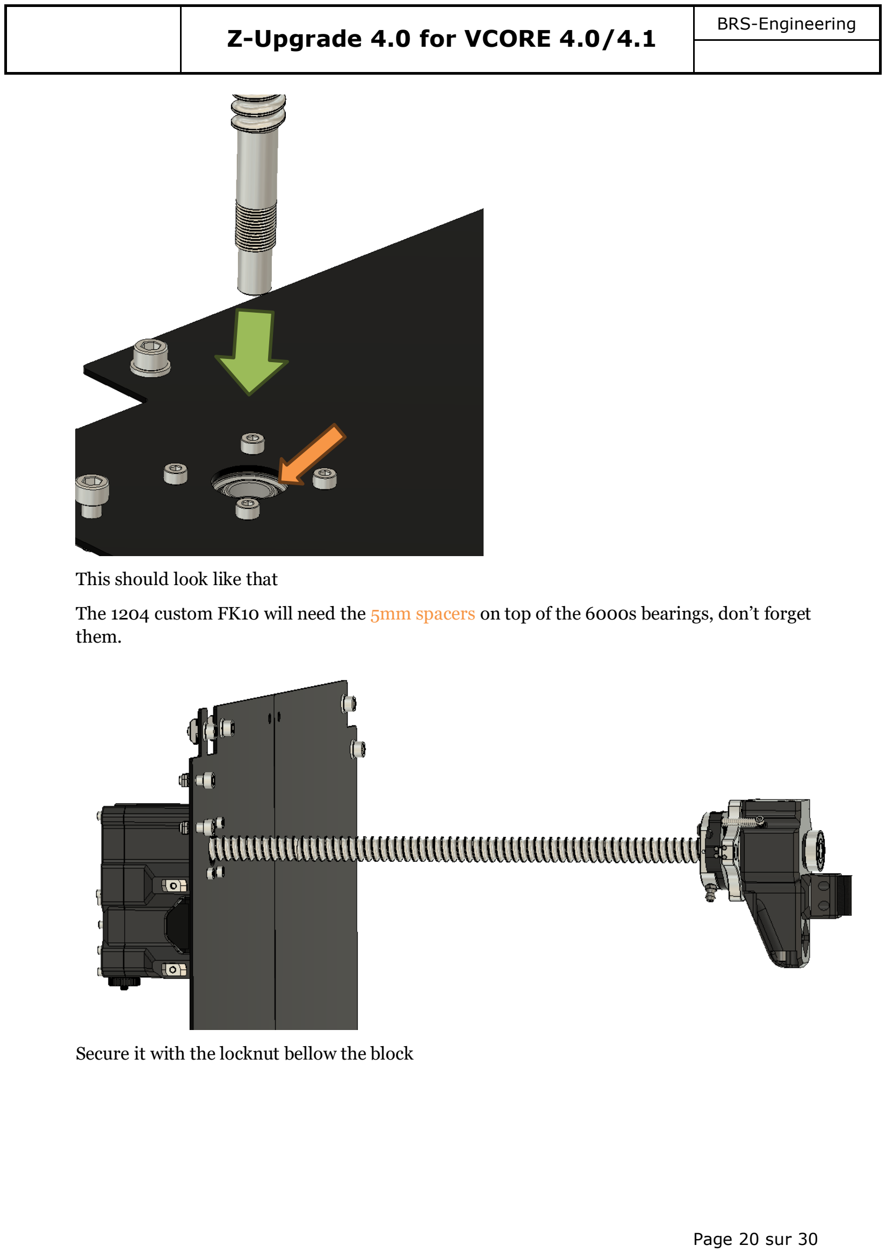
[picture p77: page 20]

Page 20 sur 30

This should look like that

The 1204 custom FK10 will need the 5mm spacers on top of the 6000s bearings, don’t forget them.

Secure it with the locknut bellow the block

### Z-Upgrade 4.0 for VCORE 4.0/4.1

Page 21 sur 30

On the last revision, DON’’T INSTALL THE LOCK NUT AND THE SPACER

In some case scenario, the locknut can induce a wobble like artifact on Z with the overconstrain applied to the spindle

As the deletion of it solve the issue, and since this locknut don’t bring anyting to the design, choice have been made to not use it

Same thing for the lower 5mm space, which is no longer needed

Locknut doesn’t have any importance here since we stand vertical, no thrust will apear so the total bed + spindle weight will do the job, and remove a potentiol source of issues

### 7 Drive closing

At this point we can take care of the drive system

Install the pulley with the belt (8mm bore for 1204/ 10mm bore for 1605)

BE CAREFUL WITH THE 60T INSERTION, DO NOT FORCE IT, ALUMINIUM CAN BE DEFORMED BY THE STEEL SPINDLE

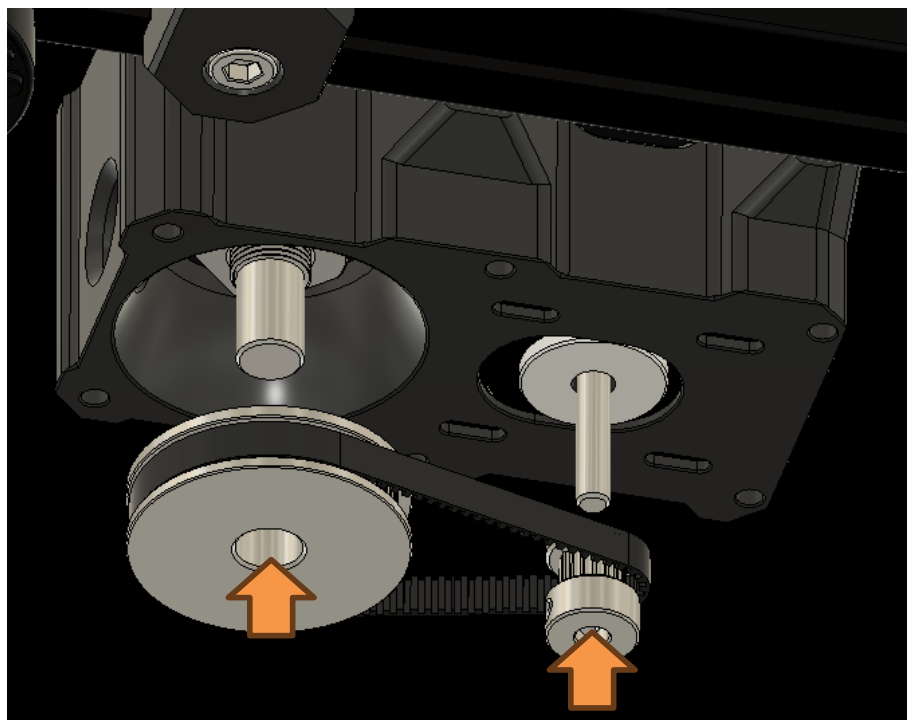
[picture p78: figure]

### Z-Upgrade 4.0 for VCORE 4.0/4.1

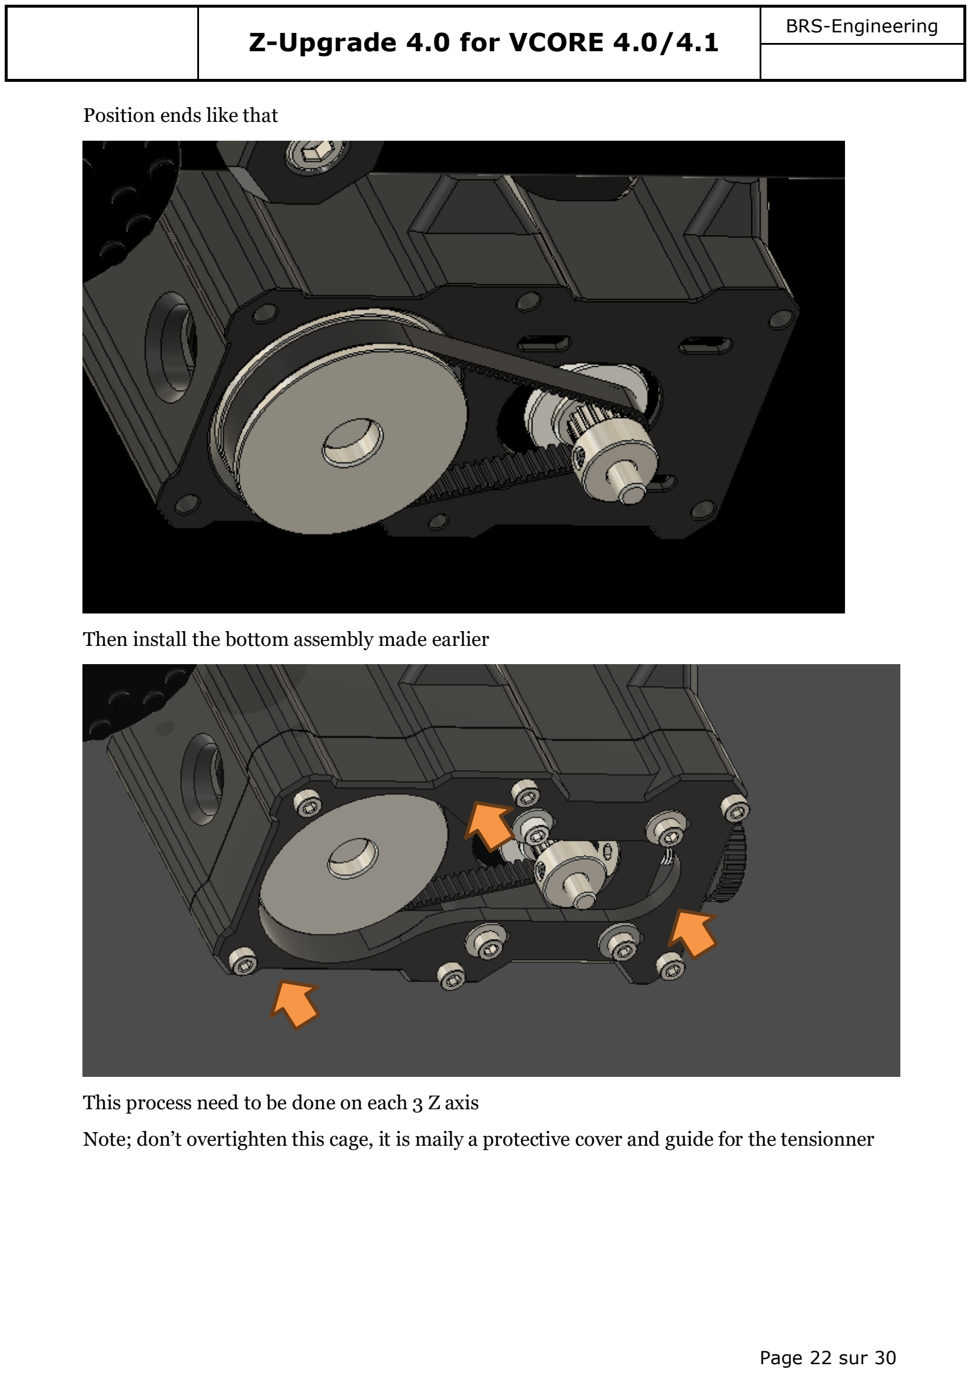
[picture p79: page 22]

Page 22 sur 30

Position ends like that

Then install the bottom assembly made earlier

This process need to be done on each 3 Z axis

Note; don’t overtighten this cage, it is maily a protective cover and guide for the tensionner

### Z-Upgrade 4.0 for VCORE 4.0/4.1

Page 23 sur 30

### 8 Arms to the HG15 carriages

For the arms, same logic than a regular VC4 kit

Use the long screw from the Ratrig kit for the 2x top retaining holes

And use 2 M4x20 on the bottom retaining hole

Exemple figure

Once installed, you can hook the springs end on the m3 screw from the arm an get the sytem ready

You should end like that

### Z-Upgrade 4.0 for VCORE 4.0/4.1

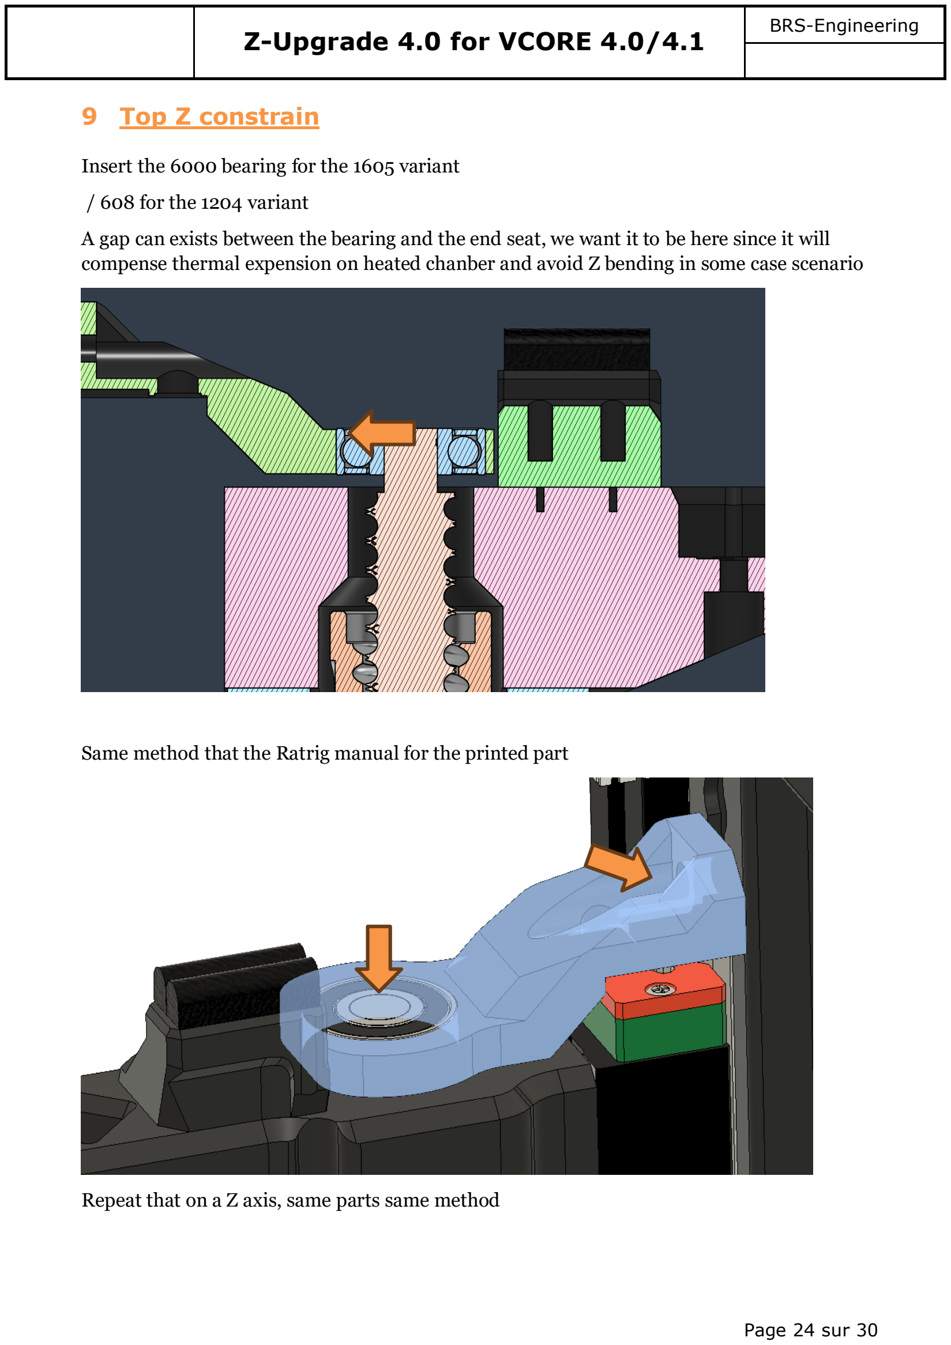
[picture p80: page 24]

Page 24 sur 30

### 9 Top Z constrain

Insert the 6000 bearing for the 1605 variant

/ 608 for the 1204 variant

A gap can exists between the bearing and the end seat, we want it to be here since it will compense thermal expension on heated chanber and avoid Z bending in some case scenario

Same method that the Ratrig manual for the printed part

Repeat that on a Z axis, same parts same method

### Z-Upgrade 4.0 for VCORE 4.0/4.1

Page 25 sur 30

### 10 Tension the Z drive

11 Push the M5 bolt to gain the minimal position.

Now tune the belt tension through the M5 Nut + washer here (Use the knob if you prefer)

We need it to be tight but do not overtension it either, we want a ferm flex on the belt.

Repeat the process with the 2 other remaining block

### 12 Final assembly

For the 1204 version, simply keep the standard stock LS/BS retainer at the top, we use the same ID 8mm bearing

In order to get some safety for potential collision, place the retainer with 2mm margin, you have the possibility to play with the retainer position

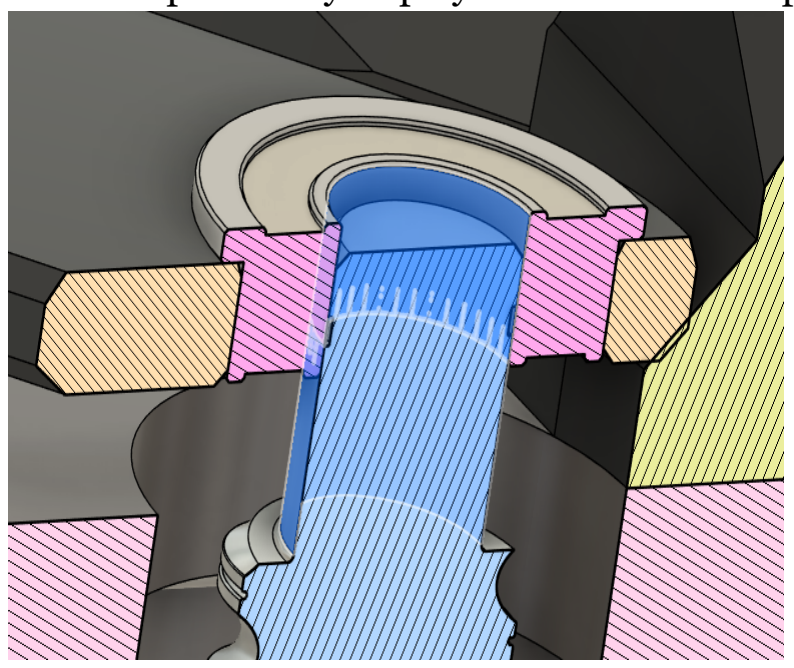
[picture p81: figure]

You can adjust a bit the height of them if necessary.

You can at this point add the bearing balls into the WobbleX assembly if not done before

### Z-Upgrade 4.0 for VCORE 4.0/4.1

1.1

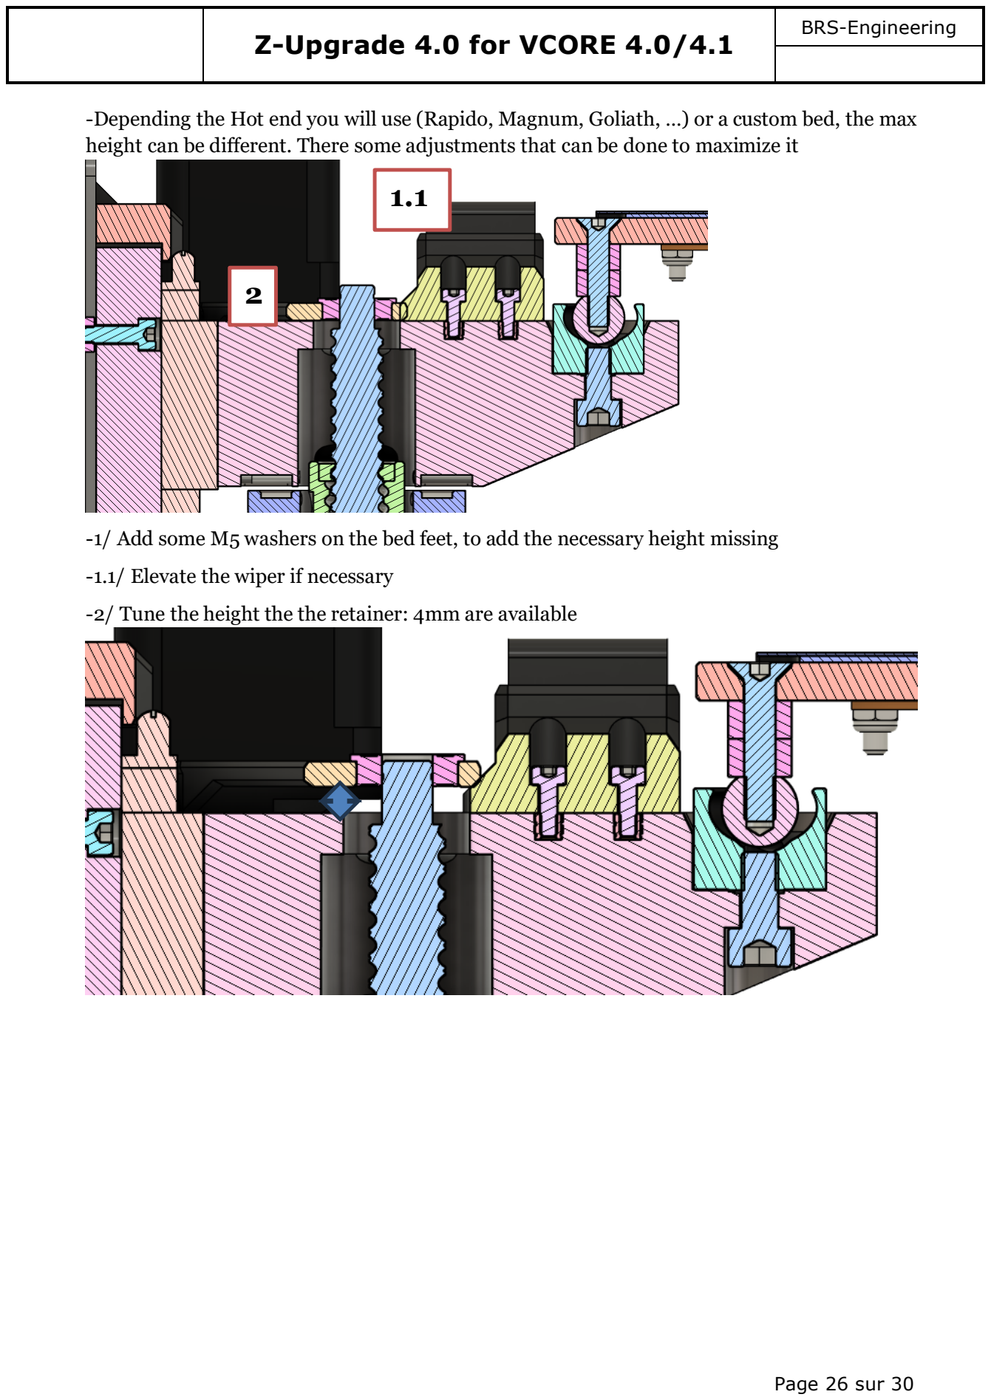
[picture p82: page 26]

Page 26 sur 30

-Depending the Hot end you will use (Rapido, Magnum, Goliath, …) or a custom bed, the max height can be different. There some adjustments that can be done to maximize it

-1/ Add some M5 washers on the bed feet, to add the necessary height missing

-1.1/ Elevate the wiper if necessary

-2/ Tune the height the the retainer: 4mm are available

2

### Z-Upgrade 4.0 for VCORE 4.0/4.1

Page 27 sur 30

### 13 Config cfg

The first thing to do is to correct the rotation_distance of all Z sections

1204: 4, transformed with the 1/3 ration to +-1.3333

1605: 5, transformed with the 1/3 ration to +-1.6666

Then we need to reverse the Z motors since they are inverted (pointing the bottom)

Simply add a “!” in front of the “dir_pin” (ex: dir_pin: !PC12)

Notes:

-In some rare scenario lowering the RUN_CURRENT on the Z motors, can improve the behaving of the system

-Remember that we do not need power here since the 60:30 reduction is working for it already

-I strongly recommend placing safe, low temp focuses settings on the TMC section of the Z motors to get perfect

-Use 16 microstep

-Keep in mind the NEMA + the 60:20 reduction + the 4-5mm per rotation motion is decupling the power of the system and can move powerful forces.

-Be careful with your fingers, your toolhead and you light gantry

-In order to avoid overdamages, the M4 insert in the block holding the whole assembly will popout to avoid issues on expensive parts like your gantry or toolhead

### 14 Troubleshooting

If you encounter some wobble issues:

The Z-Upgrade is made to LIMIT the wobbling, that mean virtually there will be some, at a certain point it is not quantifiable

The level of Z artifacts is link to the quality of the assembly

Actually the upgrade was release after a lot of test, and a lot of beta testers and tremendous unit since 2021 behave perfectly. So it works when everything is lined up accordingly

### Z-Upgrade 4.0 for VCORE 4.0/4.1

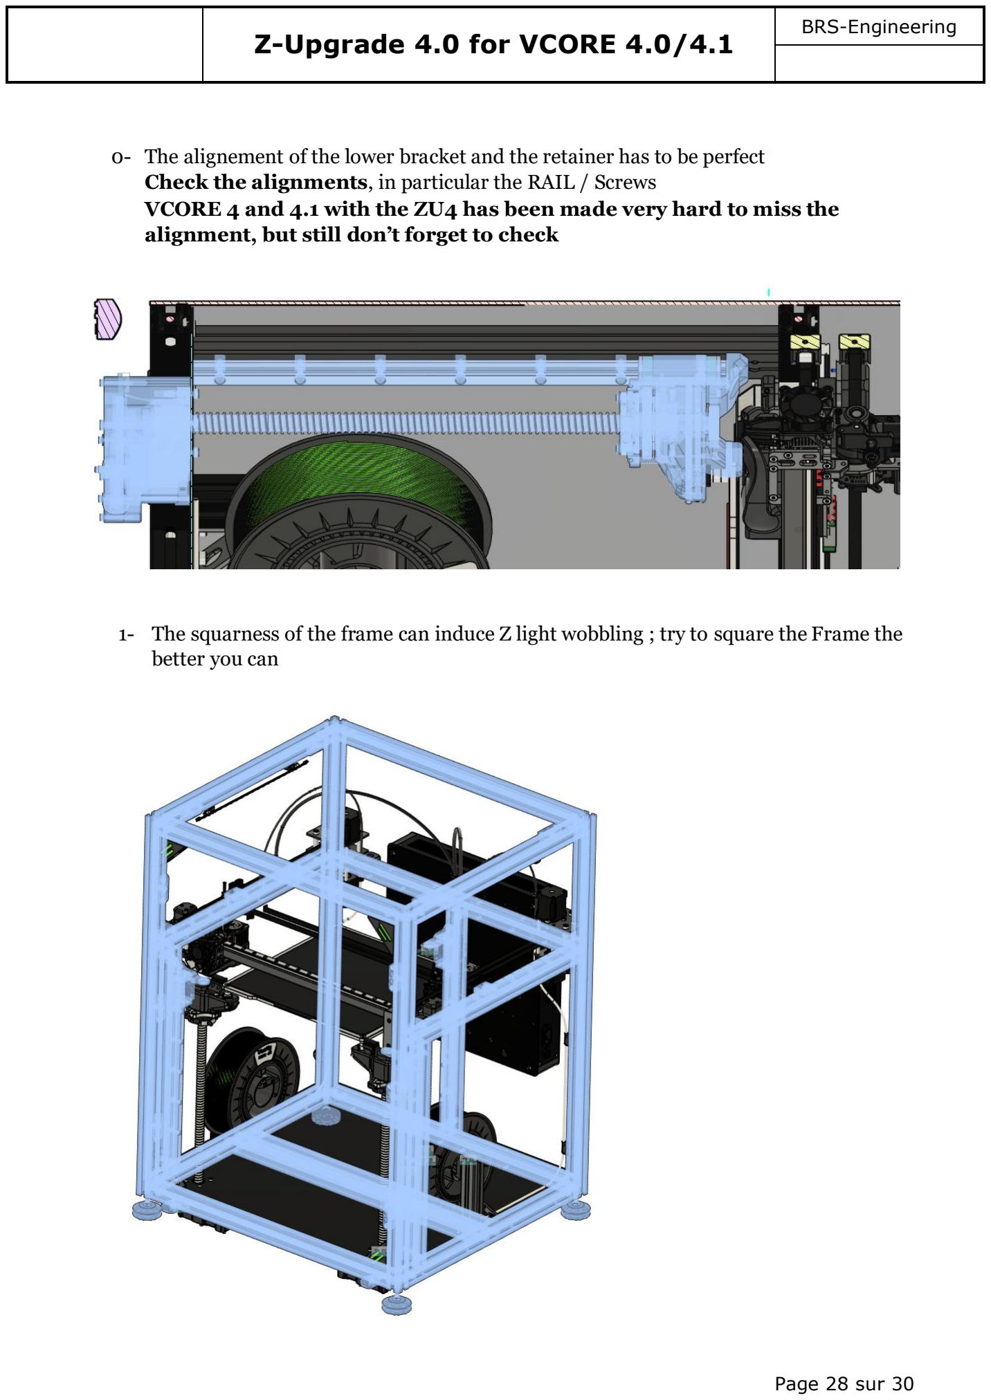
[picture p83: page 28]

Page 28 sur 30

0- The alignement of the lower bracket and the retainer has to be perfect
Check the alignments, in particular the RAIL / Screws
VCORE 4 and 4.1 with the ZU4 has been made very hard to miss the alignment, but still don’t forget to check

1- The squarness of the frame can induce Z light wobbling ; try to square the Frame the better you can

### Z-Upgrade 4.0 for VCORE 4.0/4.1

Page 29 sur 30

2- Check if the is no collision to the wobble system and the SFU Nut in the free space arounds it

Check the ball seats

3- Remove the springs; As they slightly increasing friction, it can make another issue worse, It will be working perfectly fine without, as they were meant to secure the ball seats in the system

### Z-Upgrade 4.0 for VCORE 4.0/4.1

Page 30 sur 30

3- Check the tightening of screws, nema etc

4- Hard point checks, the spindle can be rotate by hand without resistance

5- Cleanliness / lubrication checks (Rails + BS): Use a Hiwin GS04 lithium type grease or qualitative equivalent

Disclaimer

The system is designed to operate on a properly assembled Vcore. Even a slight mounting error can make it impossible to upgrade or issue during prints.

If the parts to be printed are made by the customer, check that the dimensions at the output of the printer are respected. : a bad dimension will block (+ -0.25mm) the assembly.

This kit is an optional upgrade, intended for an informed public and having advanced experience, its assembly and / or its function and / or its quality of execution are the responsibility of the customer and are not guaranteed in public view by BRS-E. BRS Engineering accepts no responsibility in the event of bad sourcing (bad quality and / or bad dimensions sfu), bad assembly by the customer, or bad assembly of the base Vcore.

The kit has proven its POC and POW in quality controls at BRS-E as well as at a beta test program, As is, the design works as expected

### 15 Assistance

If you need assistance ; I can help on:

Mail : contact@brs-engineering.com,

## Discord: BRS-ENGINEERING-Florent Broise

brsengineeringflorentbroise_3873

Meta Messenger: BRS-Engineering

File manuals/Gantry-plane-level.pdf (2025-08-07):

Gantry plane leveling procedure | BRS-Engineering

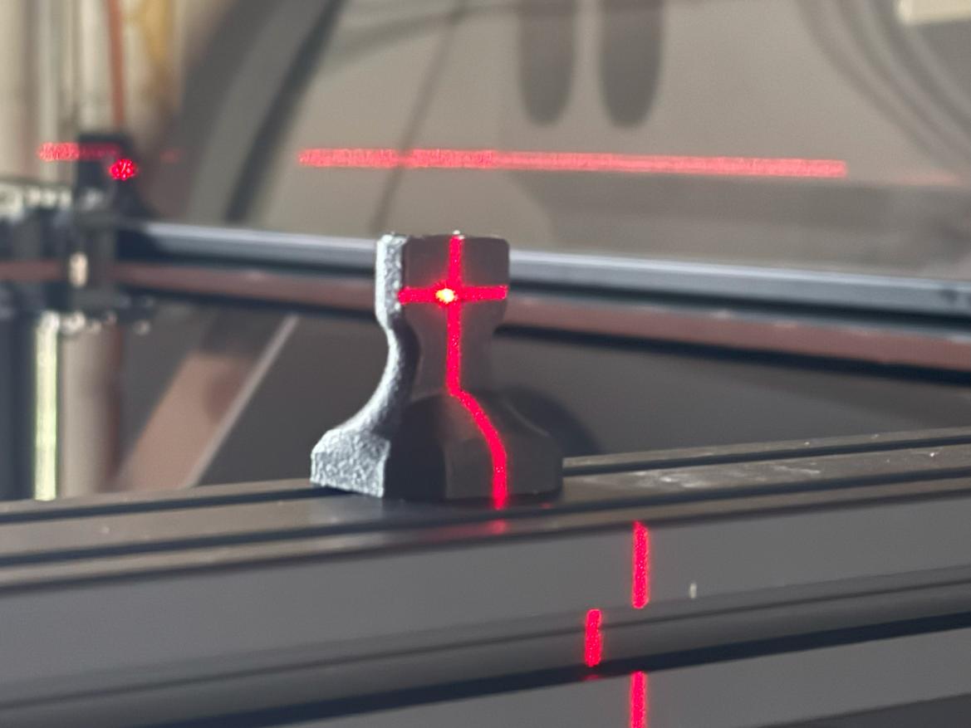
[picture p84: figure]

Page 1 sur 9

# Gantry plane leveling

### Suivi des évolutions

Indice | Date | Description de l’évolution | Auteur
0.0 | 07/08/2025 | Création | FBR

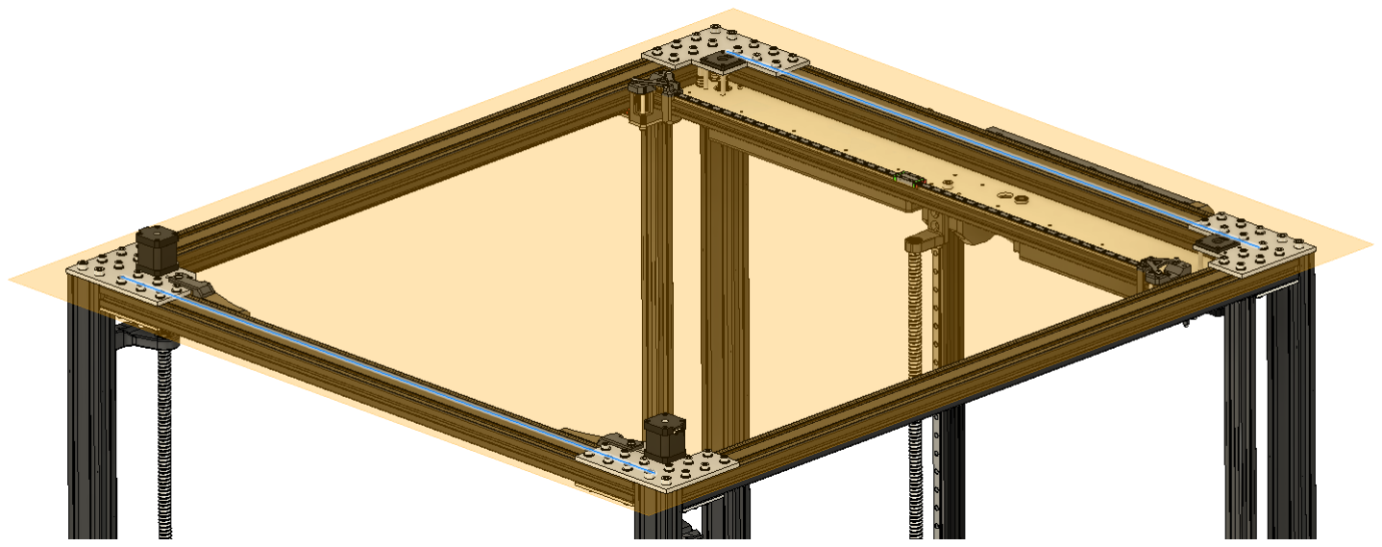
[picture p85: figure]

Page 2 sur 9

### 1 Settling

Let the machine settle on the ground where you will let it rest

This is important, since no floor is flat, we will trim to machine to this specific place

If the machine is moved afterward, it can drastically change the Mesh

### 2 Trimming the squarness

1/ The theory

Here we need the gantry plane to be flat, some variances can make it unheaven :

-Bad assambly

-Floor plane unheaven

-Flexibility of the frame

-A mix of all the previous points

What is the gantry plane ? : The plane created by the upper extrusions where the rails are moving

This plane is composed by 4 segments, which lead to a potential imprecision

Most of the time caused by a bad assambly, the floor can by beeing unheaven inducing a flex in the machine frame, leading this place to be more like a curve

A X crossbar with flatness issues on a curve will create a more complex curve with sometimes strange topology, even with perfectly flattened bed. This issue is not a bed issue, it is a gantry flatness issue. Your probe is measuring the bed, but reversly probe the gantry flatness too.

Let’s see what ane exagerate exemple can create :

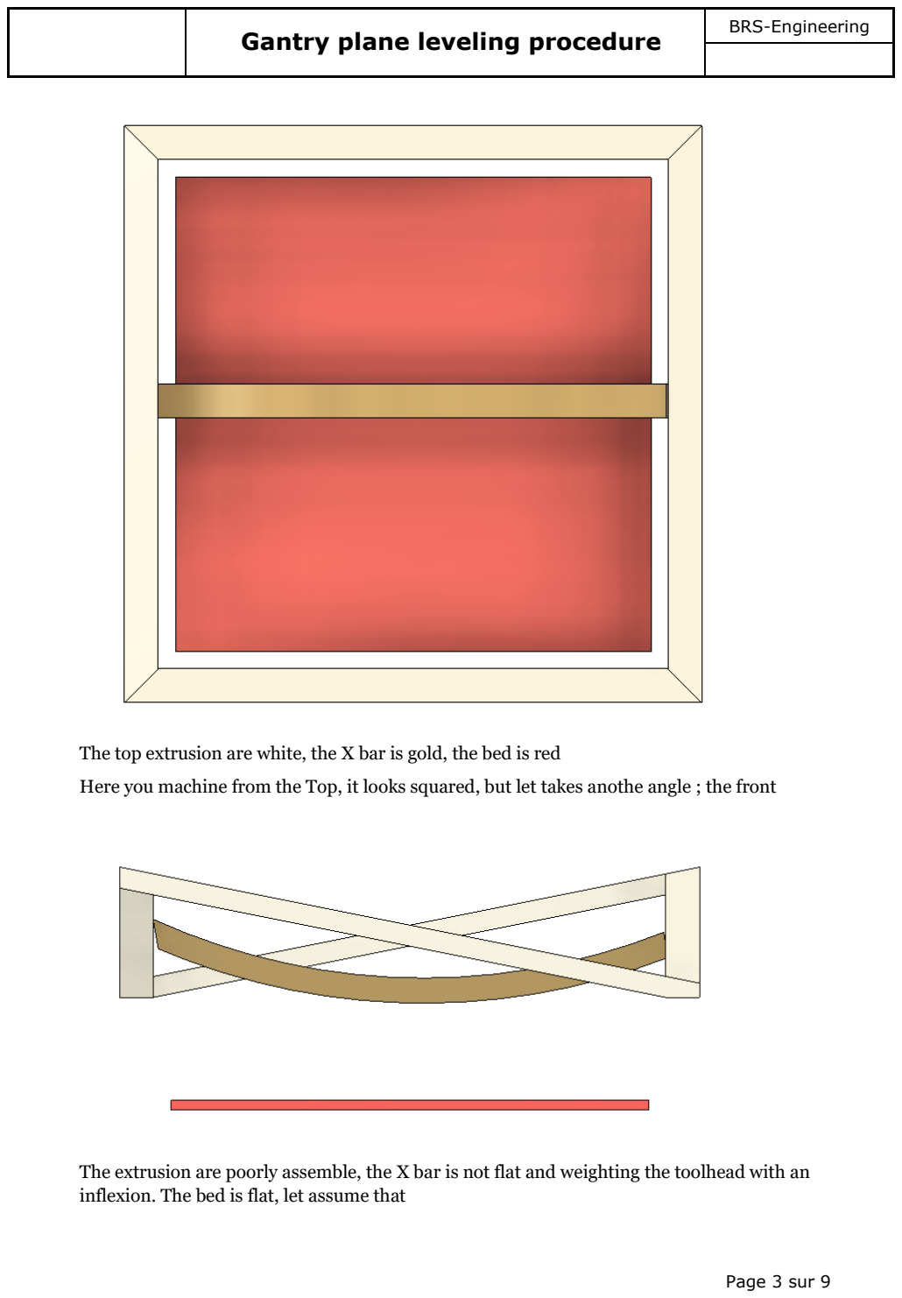
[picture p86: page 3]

Page 3 sur 9

The top extrusion are white, the X bar is gold, the bed is red

Here you machine from the Top, it looks squared, but let takes anothe angle ; the front

The extrusion are poorly assemble, the X bar is not flat and weighting the toolhead with an inflexion. The bed is flat, let assume that

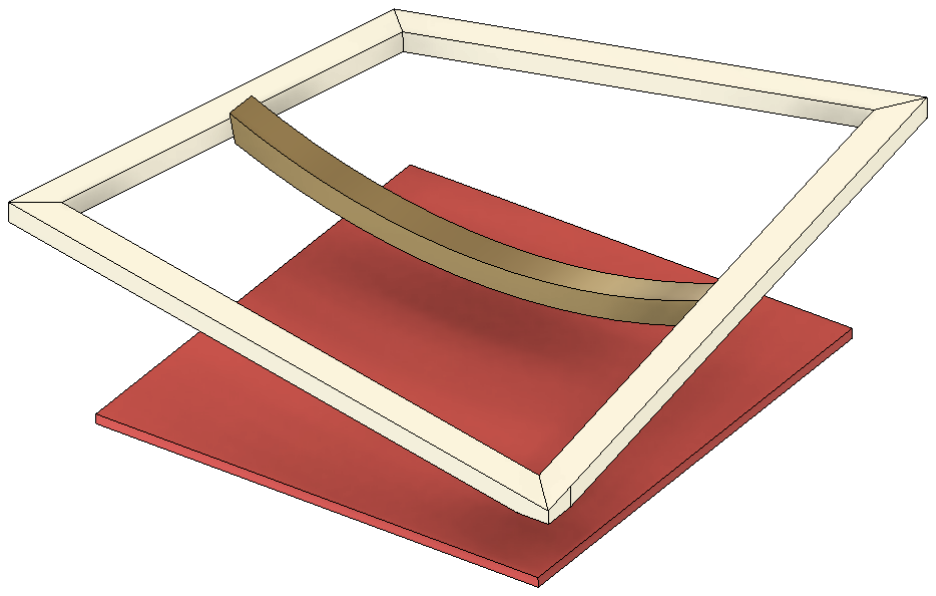
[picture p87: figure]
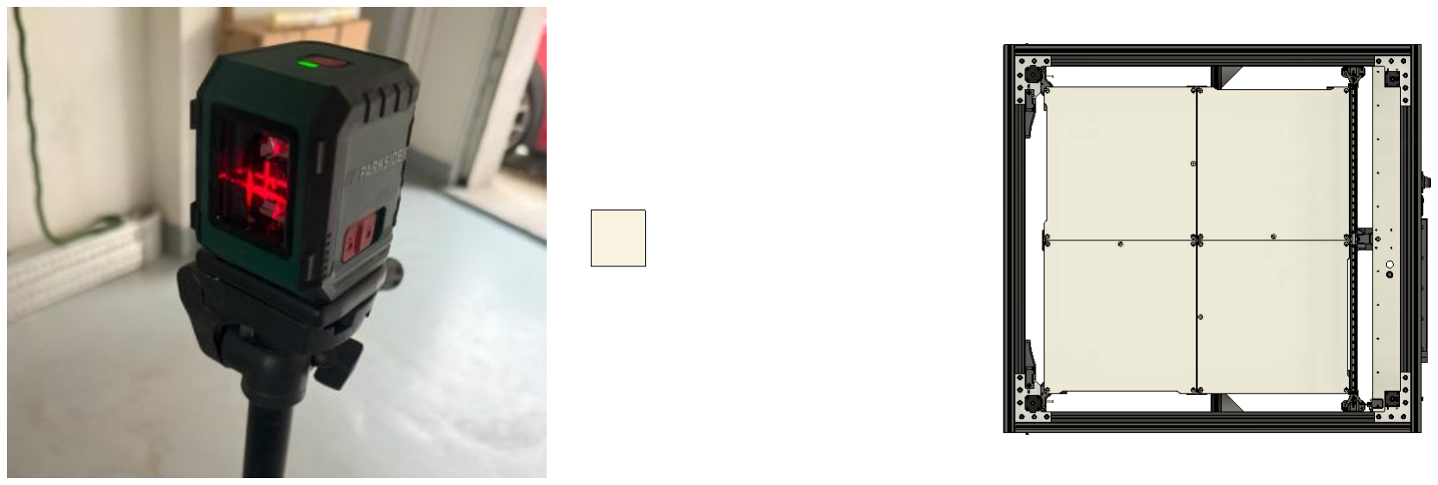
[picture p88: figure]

Page 4 sur 9

Now just imagine the probe on the toolhead moving all across the area, it will features a very bad mesh, not because of the bed, but because of the general situation.

In some case the bed is not flat either, which is a new level of issue

I even see sometime with some customer, a perfect bed mesh, but with an impossible first layer, or a bended printed part after each prints ; the reason why, 1 chance on a million, the bed imperfection matches the gantry imperfection, the mesh was fine, the reality was chaos.

2/ The trimming

You will need :

- Laser niveler (few Euros at any local discount shop)
- 5x BRS target (Target piece + M3x30mm + m3 hammer nut) (4x target minimum)
- The machine on his FINAL PLACE
- Remove any reinforced corners or bars, we need it neat

Place the laser leveler facing the machine

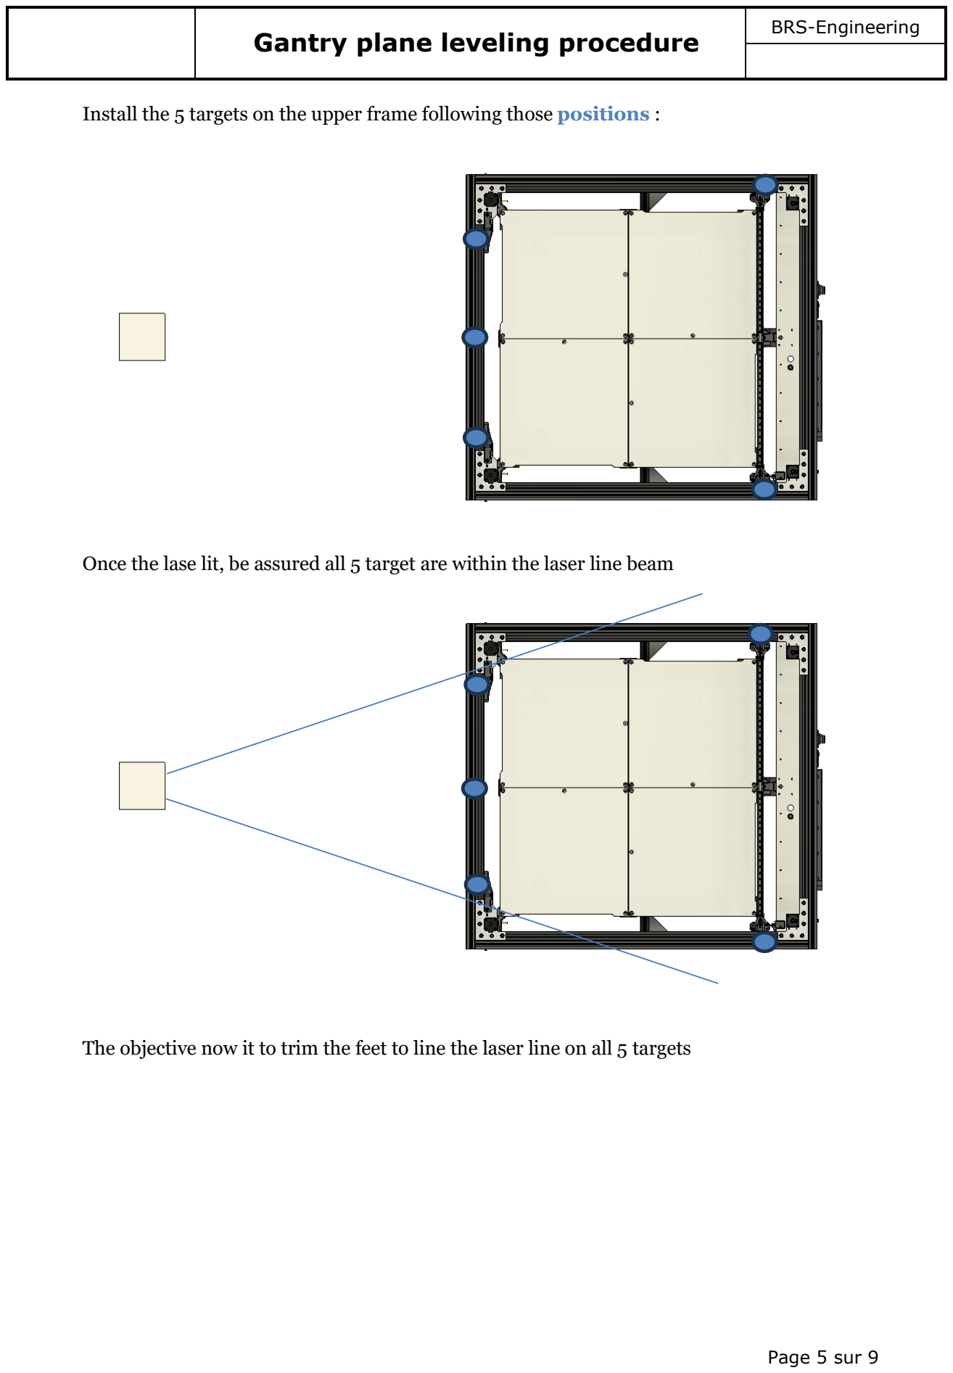
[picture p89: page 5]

Page 5 sur 9

Install the 5 targets on the upper frame following those positions :

Once the lase lit, be assured all 5 target are within the laser line beam

The objective now it to trim the feet to line the laser line on all 5 targets

Page 6 sur 9


Target pin are made of a plastic part, and a screw to fix it. An 0.2mm opening has been made to reflect the laser on the screw head, this will be the spot to lit.

Take the centre front as a référence, place the initial light on it

Then you need to assess which target are’nt on the line, trim the 4 feet accordingly to level the machine until the 5 target are aligned with the laser beam

3/ The control

-Once done, let the machine rest a bit

-Power it, Home it, make a tilt

-Recontrol the target still ligned up with the laser

Now if the gantry is flat and ligned, a Tilt will tell us the bed place it perfection parallel to this gantry plane

Lets control it :


Page 7 sur 9

Her ewe can compare the retainer level with the bed, the level is perfect


Page 8 sur 9

Your are now sure the gantry plane is flat (+-0.1mm)

4/ Rest the machine

Let the machine rest some hours, sometime the floor will work the machine a bit on the frame flexibility side

Take a new measurment of the Target 24h later

### 3 Assistance

If you need assistance ; I can help on:

Mail : contact@brs-engineering.com,

Discord: BRS-ENGINEERING-Florent Broise brsengineeringflorentbroise_3873

Meta Messenger: BRS-Engineering

Page 9 sur 9

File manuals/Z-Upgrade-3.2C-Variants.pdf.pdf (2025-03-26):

Z-Upgrade 3.2C Variants | BRS-Engineering


Page 1 sur 6

# GUIDE : Z-Upgrade 3.2c variants

### Suivi des évolutions

Indice | Date | Description de l’évolution | Auteur
0.0 | 24/03/2024 | Création | FBR

Page 2 sur 6

### 1 Objective

The Goal her is to review all ACTIVE variants of the BRS-ENGINEERING Z-Upgrade 3.2C variants to pick the one made to best fits your needs:

KEEP IN MIND THAT ALL Z-UPGRADE 3.2C VARIANTS ARE COMPATIBLE FOR ANY V-CORE 4.0 MACHINE. THIS DOCUMENT EXPLAINS YOU HOW TO WISELY CHOOSE THE BEST FOR YOUR SCENARIO.

### 2 Variant Lists

Variant | Released | Made for
Z-UPGRADE 3.2C | 30/04/24 | VCORE 4.0 (CoreXY/Hybrid) 300/400/500
Z-UPGRADE 3.2C-Reinforced arms | 21/01/25 | VCORE 4.0 (CoreXY/Hybrid) 300/400/500/++ with Custom heavy cast bed
Z-UPGRADE 3.2C-H | 17/03/25 | VCORE 4.0 (CoreXY/Hybrid) 300/400/500/++ with a taller Z volume AND/OR Custom heavy cast bed

### 3 Ballscrews size

| Z-UPGRADE 3.2C | Z-UPGRADE 3.2C-Reinforced arms | Z-UPGRADE 3.2C-H
SFU1204 | YES | NO | NO
SFU1605 | YES | YES | YES

What size should I take?

Ballscrew type | diameter (mm) | Pitch | Pros | Cons
SFU1204 | 12 | 4 | “Lighter” then 1605 Nut less wide 95% of the time sufficient to handle loads | Can be hard to find at correct prices after 1000mm (Selfsource)
SFU1605 | 16 | 5 | Very stiff and straight for long Z height Can support insane weights Easily found for long size and priced correctly | Heavy


Page 3 sur 6

There is no “performances” differences on the print quality between each SFUs type, BRS-Engineering originally offer both to meet the availability on the market, and 1605 add some insane possibility for very big or specific machines.

### 4 WOBBLEX or BRS-Oldham V3

| Pros | Cons
WobbleX | Low-profile (few mm gained on Z) Accept heavy load | Expensive
BRS-Oldham V3 | Cheaper on price | Can’t handle the same weight than WobbleX Few mm thicker (No Z loss compared to the Stock VC4)

### 5 General comparisons

Overall, all variants/editions share the same principle and the same base

The 3.2C (base) will be reference here

Keys
differences
Z-UPGRADE 3.2C | Z-UPGRADE 3.2C- Reinforced arms

Z-UPGRADE 3.2C-H

StarLock
design


Classic version with M3
inserts (1605-1204)


Classic version with M3
inserts (1605 only)

Withstands more weight

(1605 only)

Ballscrews
Type
SFU1204 or 1605 | SFU1605 | SFU1605


Page 4 sur 6

Body type


3.2C common | 3.2C common


H Revision, slighly enlarged for the bogger StarLock

Arms Type 3.2C arms OR Reinforced Arms with 2x 100mm steel
rods 5if SFU1605)

Reinforced Arms with 2x
100mm steel rods

Either 3.2C arms OR Reinforced Arms with 2x 100mm steel rods



Page 5 sur 6

Mounting


M3 | M3

M5

Decouplers

Oldham


WS12

WS16

Oldham

WS16

WS16


Page 6 sur 6

### 6 Decision tree :

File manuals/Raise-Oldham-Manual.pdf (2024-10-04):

BRS-Raise3D Oldham decoupler | BRS-Engineering


Page 1 sur 4

# BRS-Raise3D Oldham manual

### Suivi des évolutions

Indice | Date | Description de l’évolution | Auteur
0.0 | 03/10/2024 | Création | FBR

Decoupling mechanism developed to overcome wobble on the Z axis for Raise3D Pro/Pro2/Pro3* machines

### 1 Machine preparation

The Oldham need to be installed bellow the retaining plate of the heated bed

You will need tto be able to slide the rings on both 2005 ballscrew nuts

So either you rewove the heated plate + the bed underbed frame

(https://support.raise3d.com/Pro2-Series/how-to-install-the-build-plate-4-264.html)

Or you remove only the 2005 ballscrews, as you prefer


Page 2 sur 4

### 2 Preassembly

Here the order of assembly:

The Bottom ring (flanged), need to be secured to the 2005 nut with four M5x14mm screws, be careful to use short version, we don’t want the screws tips to go inside the disc effect area

The Upper ring need to be secured through the underframe structure

Be careful to insert all discs before closing this section

### 3 Assembly

Once the 2005 ballscrew tip is free, you can slide the first ring, the one with 2 longer flanges

Then secure it to the nut with 4x m5x14 (-3mm +-)

Then Slide the central ring

Bottom | Up


Page 3 sur 4

Then the upper one

Then repeat the same actions on both ballscrews


Page 4 sur 4

Once done, reinstall the underbed frame, or re-slide the ballscrew if you chose to do so

Secure the top ring to the frame with 4x m5x14mm

Position the 4x 4mm balls

### 4 Check / Disclaimer

This product is still in BETA mode

As the mechanism is thicker than the stock solution, be careful of the Z dimension of the object you want to print, which will be reduced.

The machine can’t know this fact, and you will have to reduce the max Z by 35mm

Exemple: If the printer allows 300m of Z, the max height of the part you will be able to print without collision will be 265mm

This doesnt take into consideration the eventual margin of clearance Raise 3D have placed on the machine.

I strongly advise that you make a manual check with the Bed height as a dry run to see where the real limit is

As the BETA status is still active ALL feedbacks are welcome to perfectionate the assembly and the development. ATM this mod has been tested successfully, and give a good balance between the procedure and the solution to wobble.

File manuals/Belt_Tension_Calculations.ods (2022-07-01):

 |  | URL: | https://benchtopmachineshop.blogspot.com/2019/04/printer-belt-tension.html
f0= | =1/2L | L | =SR(F/u) | =F/u | F - lb |  | F - N | F | u (6mm GT2)
28,35 | 1 | 0,5 | 28,35304535 | 803,89518072 | 1,5 | 1 | 4,44822 | 6,672330 | 0,0083
112,07 | 1,976284585 | 0,253 | 56,7060907 | 3215,58072289 | 4 | 1,5 | 4,44822 | 26,689320 | 0,0083 | Ender 3
93,88 | 1,655629139 | 0,302 | 56,7060907 | 3215,58072289 | 4 | 1,5 | 4,44822 | 26,689320 | 0,0083 | Ender 3
 |  |  | 600mm Belts
f0= | =1/2L | L | =SR(F/u) | =F/u | F - lb | F - Adj | F - N | F | u (6mm GT2)
38,58 | 0,833333333 | 0,6 | 46,30032918 | 2143,72048193 | 4 | 1 | 4,44822 | 17,792880 | 0,0083
47,26 | 0,833333333 | 0,6 | 56,7060907 | 3215,58072289 | 4 | 1,5 | 4,44822 | 26,689320 | 0,0083
54,57 | 0,833333333 | 0,6 | 65,47855346 | 4287,44096386 | 4 | 2 | 4,44822 | 35,585760 | 0,0083
 |  |  | 500mm Belts
f0= | =1/2L | L | =SR(F/u) | =F/u | F - lb | F - Adj | F - N | F | u (6mm GT2)
46,30 | 1 | 0,5 | 46,30032918 | 2143,72048193 | 4 | 1 | 4,44822 | 17,792880 | 0,0083
56,71 | 1 | 0,5 | 56,7060907 | 3215,58072289 | 4 | 1,5 | 4,44822 | 26,689320 | 0,0083
65,48 | 1 | 0,5 | 65,47855346 | 4287,44096386 | 4 | 2 | 4,44822 | 35,585760 | 0,0083
f0= | =1/2L | L | =SR(F/u) | =F/u | F - lb | F - Adj | F - N | F | u (9mm GT2)
46,30 | 1 | 0,5 | 46,30032918 | 2143,72048193 | 6 | 1 | 4,44822 | 26,689320 | 0,01245
56,71 | 1 | 0,5 | 56,7060907 | 3215,58072289 | 6 | 1,5 | 4,44822 | 40,033980 | 0,01245
65,48 | 1 | 0,5 | 65,47855346 | 4287,44096386 | 6 | 2 | 4,44822 | 53,378640 | 0,01245
f0= | =1/2L | L | =SR(F/u) | =F/u | F - lb | F - Adj | F - N | F | u (12mm GT2)
46,30 | 1 | 0,5 | 46,30032918 | 2143,72048193 | 8 | 1 | 4,44822 | 35,585760 | 0,0166
56,71 | 1 | 0,5 | 56,7060907 | 3215,58072289 | 8 | 1,5 | 4,44822 | 53,378640 | 0,0166
65,48 | 1 | 0,5 | 65,47855346 | 4287,44096386 | 8 | 2 | 4,44822 | 71,171520 | 0,0166
 |  |  | 400mm Belts
f0= | =1/2L | L | =SR(F/u) | =F/u | F - lb | F - Adj | F - N | F | u (6mm GT2)
57,88 | 1,25 | 0,4 | 46,30032918 | 2143,72048193 | 4 | 1 | 4,44822 | 17,792880 | 0,0083
70,88 | 1,25 | 0,4 | 56,7060907 | 3215,58072289 | 4 | 1,5 | 4,44822 | 26,689320 | 0,0083
81,85 | 1,25 | 0,4 | 65,47855346 | 4287,44096386 | 4 | 2 | 4,44822 | 35,585760 | 0,0083
f0= | =1/2L | L | =SR(F/u) | =F/u | F - lb | F - Adj | F - N | F | u (9mm GT2)
57,88 | 1,25 | 0,4 | 46,30032918 | 2143,72048193 | 6 | 1 | 4,44822 | 26,689320 | 0,01245
70,88 | 1,25 | 0,4 | 56,7060907 | 3215,58072289 | 6 | 1,5 | 4,44822 | 40,033980 | 0,01245
81,85 | 1,25 | 0,4 | 65,47855346 | 4287,44096386 | 6 | 2 | 4,44822 | 53,378640 | 0,01245
f0= | =1/2L | L | =SR(F/u) | =F/u | F - lb | F - Adj | F - N | F | u (12mm GT2)
57,88 | 1,25 | 0,4 | 46,30032918 | 2143,72048193 | 8 | 1 | 4,44822 | 35,585760 | 0,0166
70,88 | 1,25 | 0,4 | 56,7060907 | 3215,58072289 | 8 | 1,5 | 4,44822 | 53,378640 | 0,0166
81,85 | 1,25 | 0,4 | 65,47855346 | 4287,44096386 | 8 | 2 | 4,44822 | 71,171520 | 0,0166

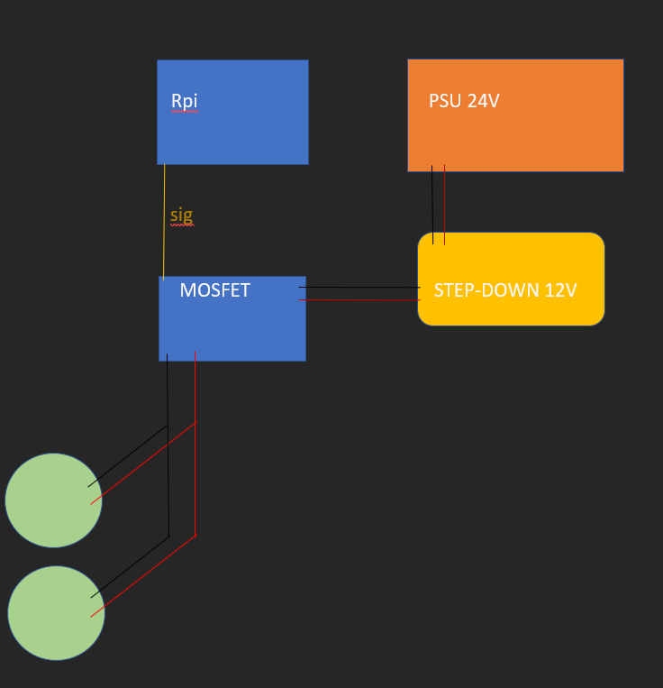
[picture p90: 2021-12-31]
image/BRSVSwiring.png

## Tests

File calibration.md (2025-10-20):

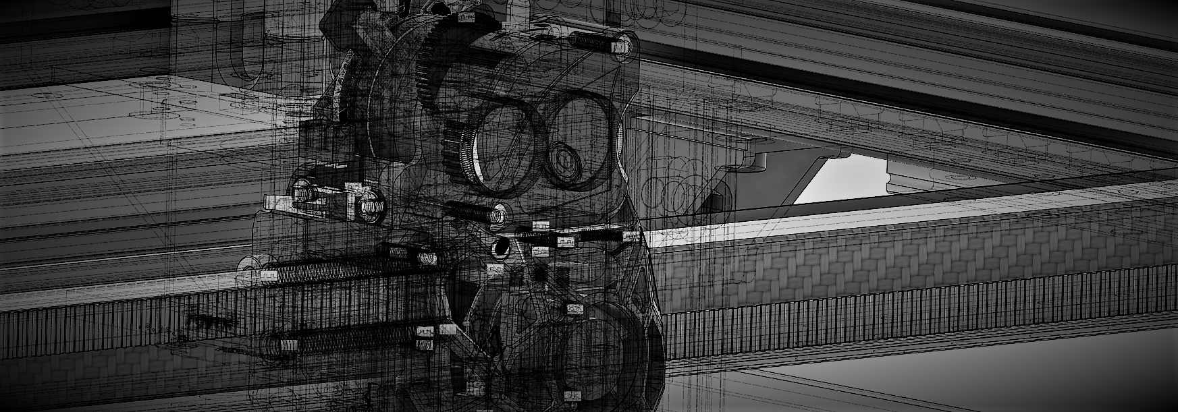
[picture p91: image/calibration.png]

# CALIBRATION OF YOUR MACHINE
## 1. Motor SYNC (AWD only)
[How to](https://www.youtube.com/watch?v=so9oqJyirKY)
Improve drastically the print quality, noise and Input-shaper

## 2. EXTRUDER Rotation_Distance
Objective|Setting|Comments|Link
-------|-------|-----------------|-------
Getting the good extrusion|Rotation_Distance|mark the filament at 120mm from your extruder, Extrude 100mm, make the calculation to retrieve the good number, TeachingTech webstite include the step/mm calculation, then use my table to get the conversion into Rotation_distance units|[Calculation](https://teachingtechyt.github.io/calibration.html#esteps) [Conversion Table](https://docs.google.com/spreadsheets/d/1FKyyWfHV8zdZKKFCmgh5MvTFCjXNV37kUfqWGvWRDxo/edit#gid=0)

## 3. Flow
Objective|Setting|Comments|Link
-------|-------|-----------------|-------
Getting the good width|Flow (Slicer)|Print a 30x30mm cube in vase mode, check the width of the layer |[Calculation](https://teachingtechyt.github.io/calibration.html#flow) [Conversion Table](https://docs.google.com/spreadsheets/d/1FKyyWfHV8zdZKKFCmgh5MvTFCjXNV37kUfqWGvWRDxo/edit#gid=0)

## 4. Adjusting belts tensions.
Section|Setting|Recommended Value|details|Calculation sheet
-------|-------|-----------------|------- |-------
Getting Equalize on the CoreXY principle|Rotation_Distance|Follow the [Instruction](/manuals/belt.pdf)|[Spectroid](https://play.google.com/store/apps/details?id=org.intoorbit.spectrum&hl=fr&gl=US) | [Download](/manuals/Belt_Tension_Calculations.ods)

## 4. Octogone Calibration for XY
Objective|Setting|Comments|Link
-------|-------|-----------------|-------
Getting Equalize on the CoreXY principle|Belt-tension+Print+Rotation_Distance|Print the [Octogon](/cad/octogon.stl) and follow the [Instruction](/manuals/calibration.pdf)|[Conversion Table](https://docs.google.com/spreadsheets/d/1PNDpxMo82B2Yi7_REPhKj44IOn1BJzk-KYgN7mVPe6Q/edit?usp=sharing)

## 5. Z Calibrations
Objective|Setting|Comments|Link
-------|-------|-----------------|-------
Getting the good Z Height|Rotation_Distance|Print a normal 30x30 cube, I personnaly use a raft to absorb the first layer thickness imprecision, mesure it and use the conversion table to find the good value| [Conversion Table](https://docs.google.com/spreadsheets/d/1FKyyWfHV8zdZKKFCmgh5MvTFCjXNV37kUfqWGvWRDxo/edit#gid=0)

## 5. Bed Mesh tips to master first layer
Objective|Advices
-------|-------
Master a perfect first layer|Use a Beacon or Cartographer probe type with 150; 150 scan points
------------------------
#|Steps|Link
-------|-------|-------
1|Implement you Probe settings with the correct offsets from the nozzle|
2|Add the Axis twist configuration to you machine|[Klipper Axis twist](https://www.klipper3d.org/Axis_Twist_Compensation.html)
3|Heat soak the bed to 80°C, Heat the nozzle to 200°C, HOME, Z-TILT, Axis twist procedure form the above link for X and Y, SAVE_CONFIG|
4|Heat soak the bed to 80°C, Heat the nozzle to 200°C, HOME, Z-TILT, Make you BED MESH calibration, SAVE_CONFIG|
5|Start a print, baby step the Z to match the perfect layer thickness. SAVE|

This would be the best procedure to get it work with precision

____________________________________________________________________________________  

Special Thanks to the helpfull content of Mickael from TeachingTech

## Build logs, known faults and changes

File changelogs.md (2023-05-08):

## 1/ L3VER Systems

- M1
Belt tensionner

Version|Description|Changelog|Date
-------------|-----------|-----------|-----------
**V1.1**|<br> M1 1.1 GT2 tensionner|[PDF](/patch/Changelog-L3VER-M1.pdf)| 01/05/23

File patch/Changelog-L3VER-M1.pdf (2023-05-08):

## L3VER M1 1.1 Changelog

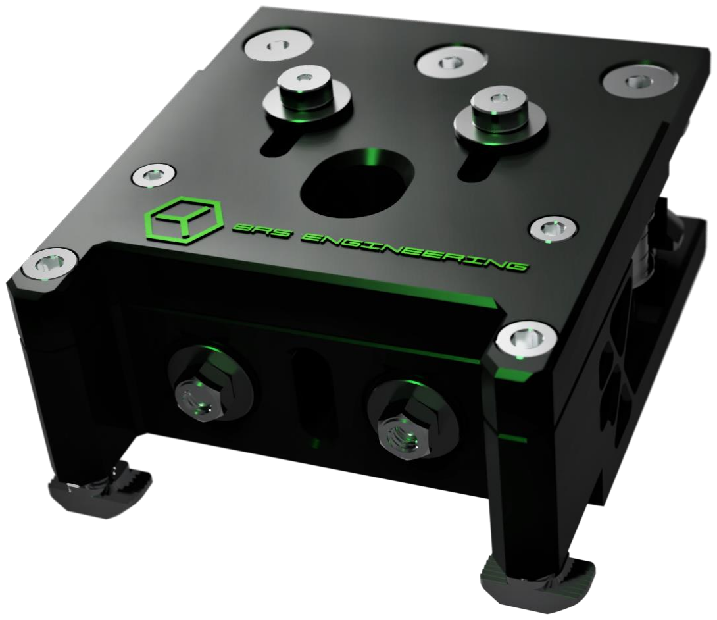
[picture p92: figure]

Page 1 sur 4

# Changelog Tensionner L3VER M1

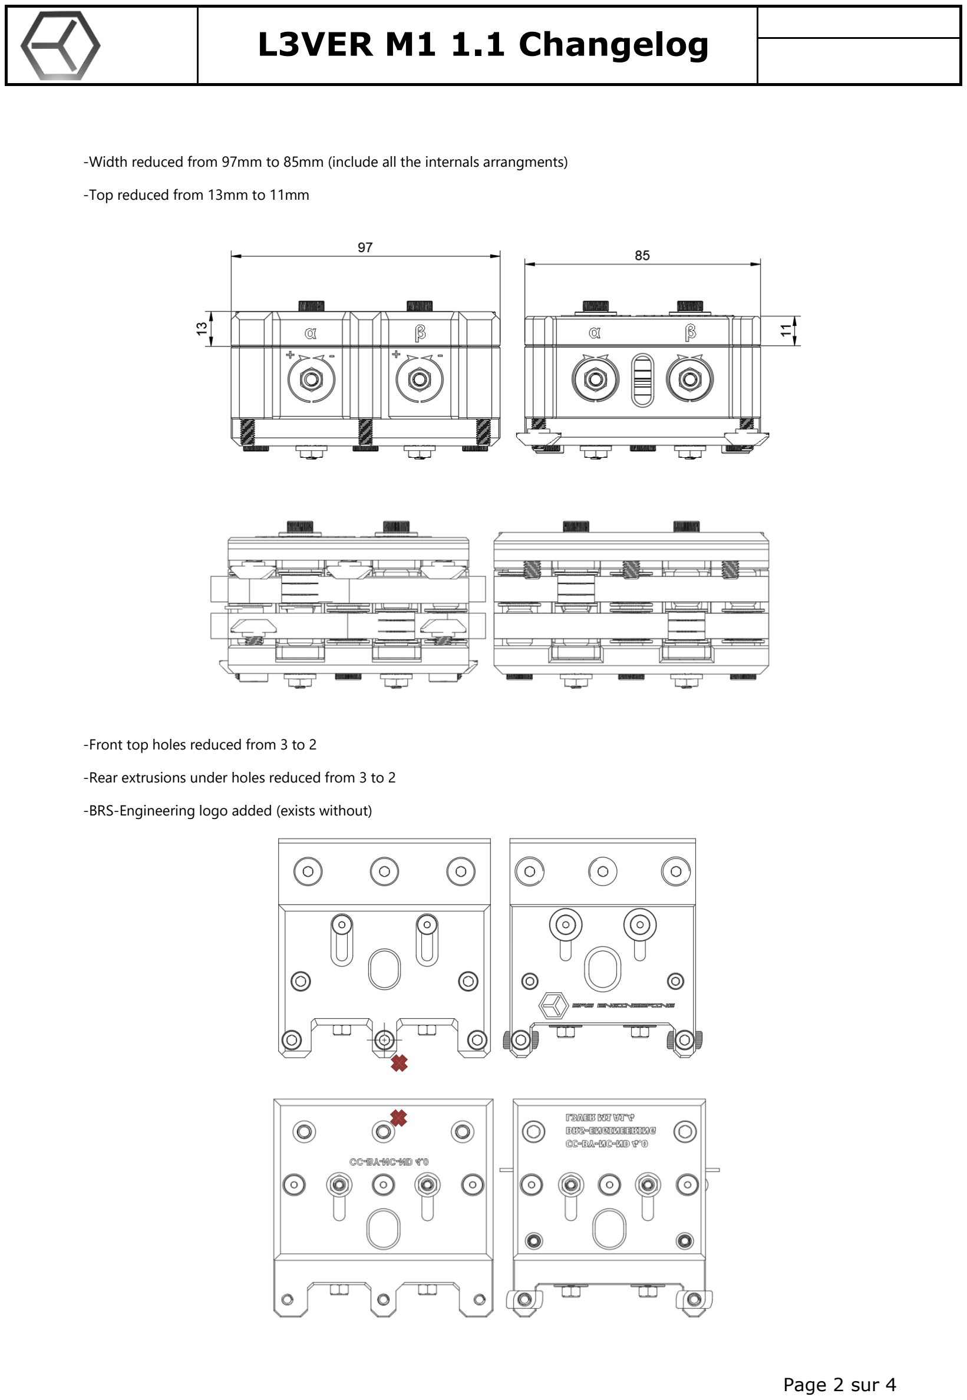
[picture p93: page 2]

Page 2 sur 4

-Width reduced from 97mm to 85mm (include all the internals arrangments)

-Top reduced from 13mm to 11mm

-Front top holes reduced from 3 to 2

-Rear extrusions under holes reduced from 3 to 2

-BRS-Engineering logo added (exists without)

Page 3 sur 4

-Internal structure modified, some excess have been removed via topology study (Less heavy on the material needs)

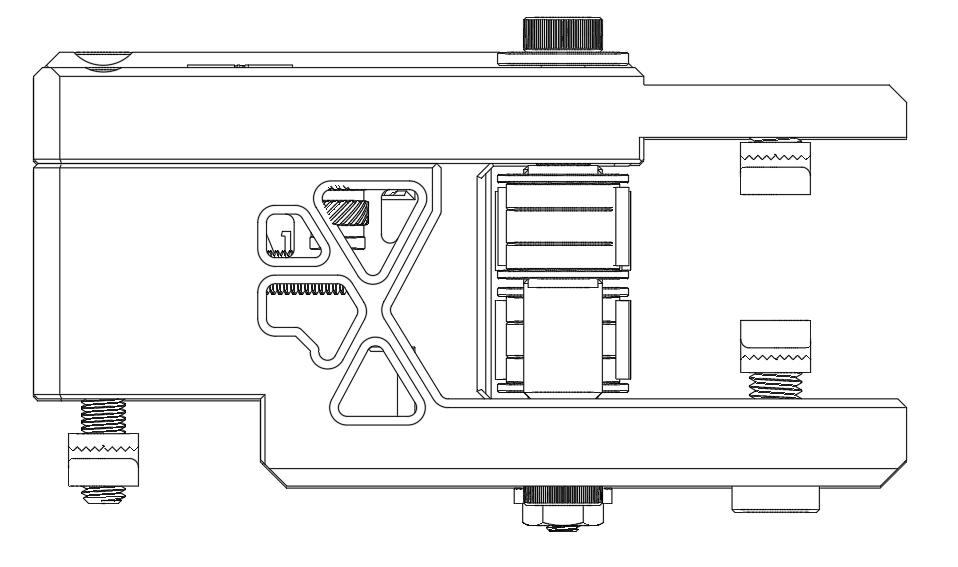
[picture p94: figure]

Some Washers has been added, looking absent on the first 1.0 STEP, but installed on the 1.0 orders from the store.

Page 4 sur 4

Any question or issue can be submited to Florent Broise on Facebook or at contact@brs-engineering.com

10-License :

This upgrade is part of the Creative commons CC BY-NC-ND 4.0, All rights are exclusive to Florent BROISE / BRS-TECH.

For a request concerning a particular case, only Florent BROISE / BRS-TECH can agree to a derogation. Feel free to ask

Right of use, sharing, PROHIBITION of commercial use and modification For more details, follow this link.

https://creativecommons.org/licenses/by-nc/4.0/

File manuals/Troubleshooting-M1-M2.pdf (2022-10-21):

### Troubleshooting L3VER M1/M2/PMB Motor block with tensionner

Page 1 sur 6

# Troubleshooting for L3VER M2/M1/PMB motor blocks

### Suivi des évolutions

Indice | Date | Description de l’évolution | Auteur
0.0 | 21/10/2022 | Création | FBR

### Preliminary checks

First we have to acknowledge few things in order to validate a good base for the M1 or the M2/PMB to operate normally

M1

-The Frame is squared

-The Belts are straignts (RR ones tends to be curved on few experiences, use a Genuine GATE LL GT2)

-The head motion without the M1 is fluid, without hard point.

M2/PMB

-The Frame is squared

-The Belts are straignts (RR ones tends to be curved on few experiences, use a Genuine GATE LL GT2)

-The 55mm rod used is a straight stainless steel one (Straight here is important)

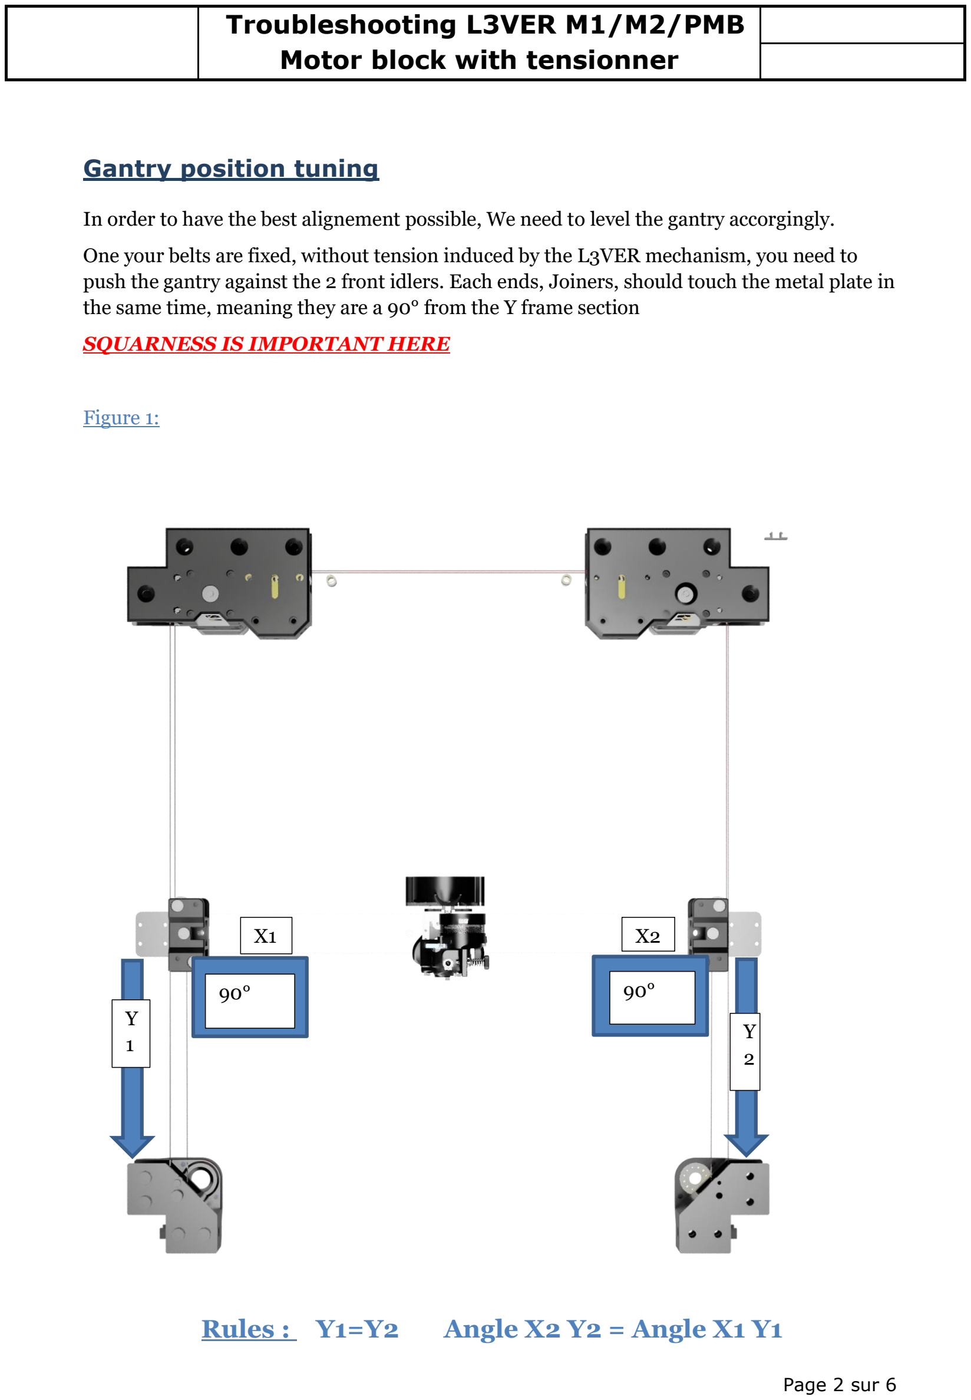
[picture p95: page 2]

Page 2 sur 6

### Gantry position tuning

In order to have the best alignement possible, We need to level the gantry accorgingly.

One your belts are fixed, without tension induced by the L3VER mechanism, you need to push the gantry against the 2 front idlers. Each ends, Joiners, should touch the metal plate in the same time, meaning they are a 90° from the Y frame section

SQUARNESS IS IMPORTANT HERE

Figure 1:

Rules : Y1=Y2 | Angle X2 Y2 = Angle X1 Y1
90° | 90°
Y
1

Y
2
X1 | X2

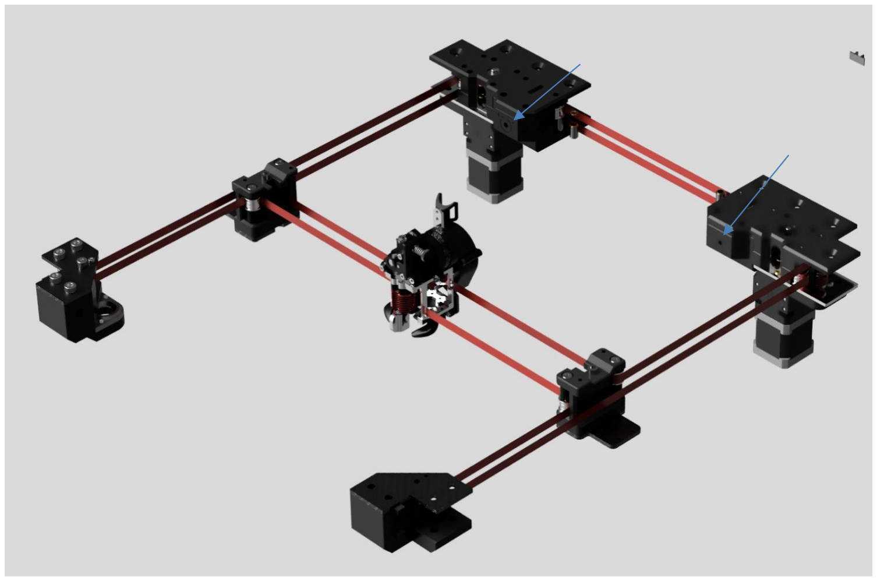
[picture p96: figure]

Page 3 sur 6

At this point you can apply pre-tension with the 2 Lever screws (M5) and tense the belts enough to not be loosed

Check if the gantry move from this 90° state, each end should be at the same level, or distance be the same. You need to understand that the tension of one module can modify both angle in the same time. You have to be cautious and precise about it to reach the perfect spot.

Apply the tension symetrically to keep an equilibrate tension, use the BRS Belt tensionning procedure (https://github.com/FlorentBroise/BRS-Printers-Mod/blob/main/manuals/belt.pdf) (https://github.com/FlorentBroise/BRS-Printers-Mod/blob/main/manuals/belt.pdf)

to apply the good one depending the size of your machine.

Don’t forget to move the head across the printed area to spread the tension

Onve done, check if the gantry is still straight over the idlers and respect the figure 1

If yes; go the the next chapter

If no: equilibrate the distance by only modifying the tension of one lever side, if it make it bigger, use the other one, until the distance are equal

Note: Having different lever tensions values is not an issue, at the end only the belt tension are important, measured by spectroid, it can be different across both modules because of the length used in the making, or the pretension applied in the first place.

Page 4 sur 6

### Main mechanical potential issues

1/ when I move the tool head across X, I feel a great continuous resistance

-Check if the belt is not rubbing at some point against something

-Are all the bearings free to roll?

-Are the Bearing stack assembly made correctly: All shims are here?

-All the bearing are ok?

-Does the L3VER 55mm shaft correctly installed?

-Does the toothed pulleys at the good height?

2/ when I move the tool head across Y, I feel a great continuous resistance

-Check if the belt is not rubbing at some point against something

-Are all the bearings free to roll?

-Are the Bearing stack assembly made correctly: All shims are here?

-All the bearing are ok?

-Does the L3VER 55mm shaft correctly installed?

-Does the toothed pulleys at the good height?

3/ when I move the tool head across X, I feel a repetitive resistance

-All the bearing are ok?

-Does the L3VER 55mm shaft correctly installed? Is it bent?

-Are the 625zz correctly installed, are they in good condition?

-Check the assembly alignment Motor/Coupler/shaft/625zz/pulley/625zz

If this alignment is not good, a precession can occurs and give those looped resistances

4/ when I move the tool head across Y, I feel a repetitive resistance

-All the bearing are ok?

-Does the L3VER 55mm shaft correctly installed? Is it bent?

-Are the 625zz correctly installed, are they in good condition?

-Check the assembly alignment Motor/Coupler/shaft/625zz/pulley/625zz

If this alignment is not good, a precession can occurs and give those looped resistances

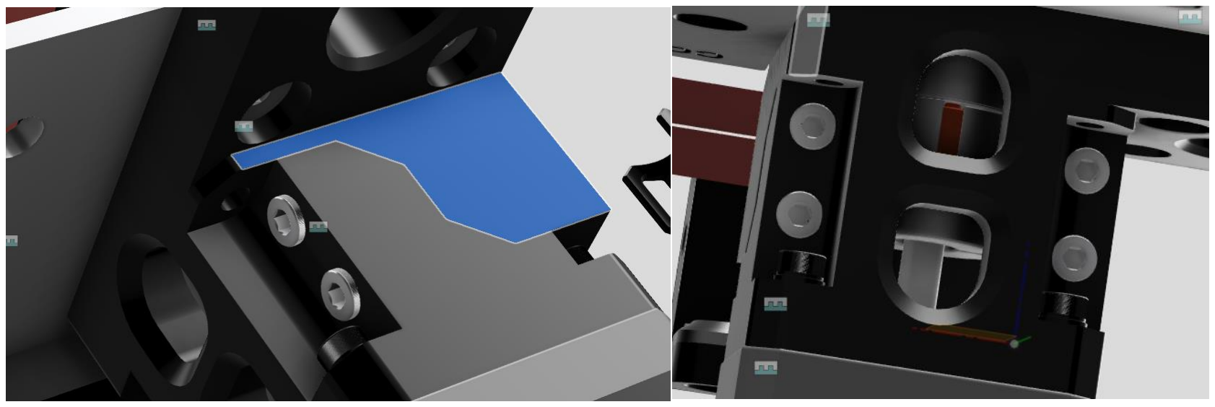
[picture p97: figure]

Page 5 sur 6

### Methods to investigate

To ensure the good Lever assembly alignment, untight the coupler on one end, in order to allow a free move from the shaft

You can do 45° head motion to isolate the motion on a specific lever block and focus the issue search here. It divides by 2 the items to check, and gives indications about which side is potentially faulty.

At this point repeat the head motion by hand, If the 1/ or 2/ is still happening, check the belt paths, something is either not free to move, or rub the frame/printed part when moving

If you have the 3/ or 4/, look for a shim missing a Lever module not correctly assembled, or a defective bearing

If you don’t have 1/, 2/, 3/ or 4/, the stepper give a rotational resistance over the shaft, meaning either the join picture here is too tight, too loose, or have not enough tolerances to match coaxiality

Try to screw or unscrew the 4 m3x30 screw to tune this coaxiality

You can use a sandpaper to remove a bit of material on the edges (explained in the PMB manual)

Make shure the couple is centered in the middle of the 2 shaft (motors and pulleys)

*You can easily confirm if the shaft is not driven properly by checking a precession during the rotation at his end on the top Lever/PMB plate

### Input shaper

At this point, the M1/M2/PMB haven’t shown issues induced to the shaper measuring tool, by his nature

That said, all loosed parts, screws, shafts, can induce vibrations and cause issues or spikes to the shaper graphs

You need to be sure everything is tight correctly, like every singles part of the printer, especially moving part.

In instance to avoid any issues with the shaper, once the tightening of the belt is made and have settled over time (few days), don’t forget to tight back the top m4 nyloc nut to lock the bolt in place.

Page 6 sur 6

This troubleshooting guide has been made upon personal experiences on those module, and customers feedback, solved atm. If you encounter an issue, you can contact me !

Thanks for following this document

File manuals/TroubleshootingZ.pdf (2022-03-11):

### Troubleshooting Z-Upgrade

Page 1 sur 6

# Troubleshooting

### Suivi des évolutions

Indice | Date | Description de l’évolution | Auteur
0.0 | 05/01/2022 | Création | FBR

### 1-Intro

The Z-Upgrade is made to LIMIT the wobbling, that mean virtually there will be some, at a certain point it is not quantifiable

The level of Z artifacts is link to the qulity of the assembly

Actually the upgrade was release after a lot of test, and a lot of beta testers

So it works when everything is lined up

Rédacteur | Responsable X | Qualité
FBR | FBR | FBR

Page 2 sur 6

### 2-Potential issues in the system

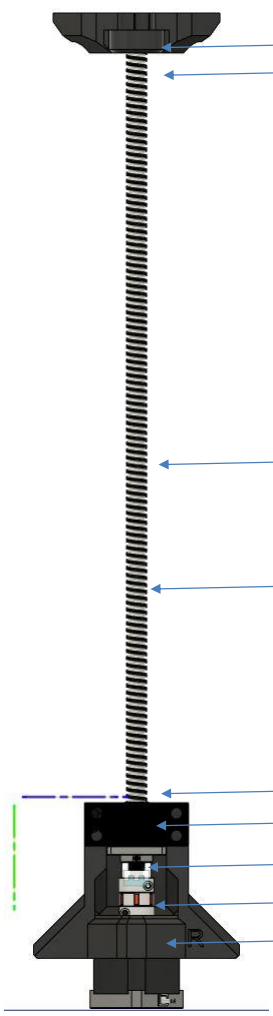
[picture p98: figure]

Bad part alignement

Bad bearing

Bad SFU1204

Bad bearing

Bad spacers positions

SFU not greased

The nut is to tight on the BK10

Bad coupler

Bad Alignement

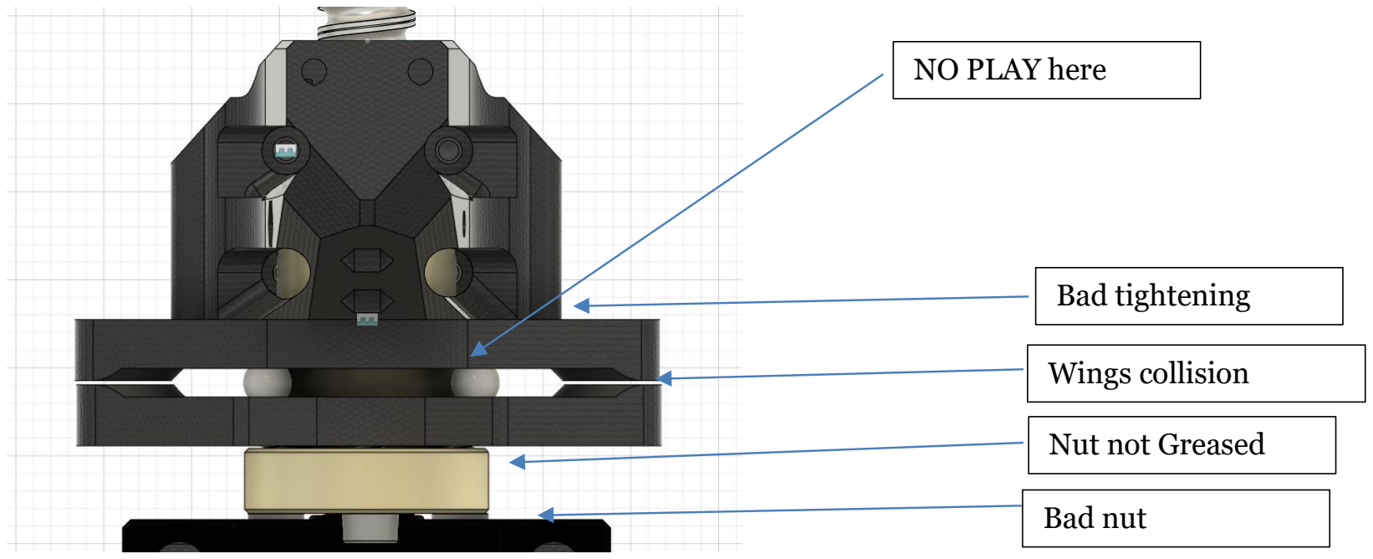
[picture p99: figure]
Bad tightening; Wings collision; Nut not Greased; Bad nut; NO PLAY here

Page 3 sur 6

### 3-Tweaks and tips

-The lower part of the coupler SHOULD NOT touch the NEMA top

-The coupler can be faulty ; you can solve the issue by separating a bit the spider from each Aluminium parts

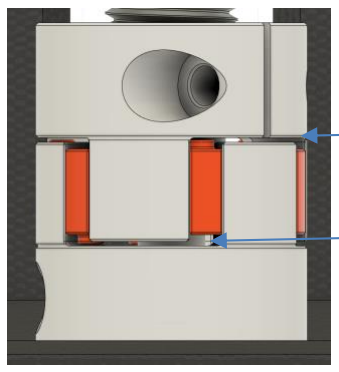
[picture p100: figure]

-Remove the circlip at the machined tip at the top of the retainer bearing

-Screws must be tightened

-A light ball lubrification can be made

+- 1.5mm

+- 1.5mm

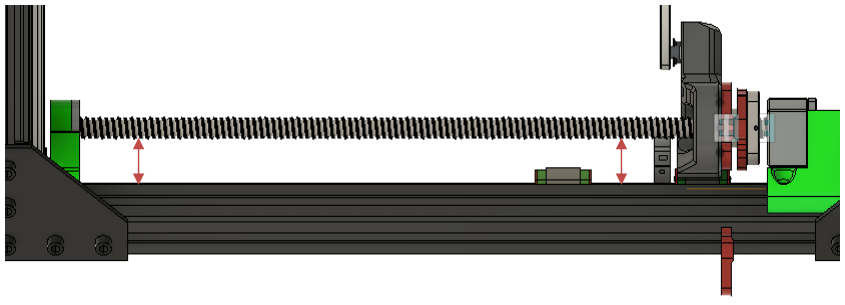
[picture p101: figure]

Page 4 sur 6

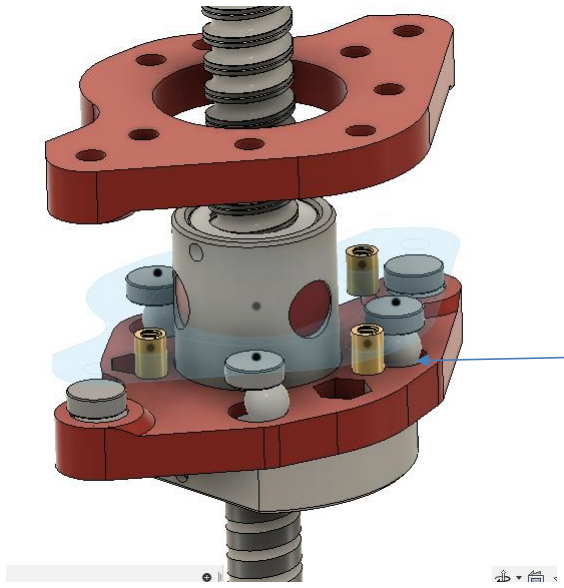
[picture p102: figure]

-The alignement of the lower braket and the retainer has to be perfect

- The squarness of the frame can induce Z light wobbling ; try to frame the Frame the better you can

A drop of oil can help

Page 5 sur 6

-Wings has to be parallele and no play should be found in it

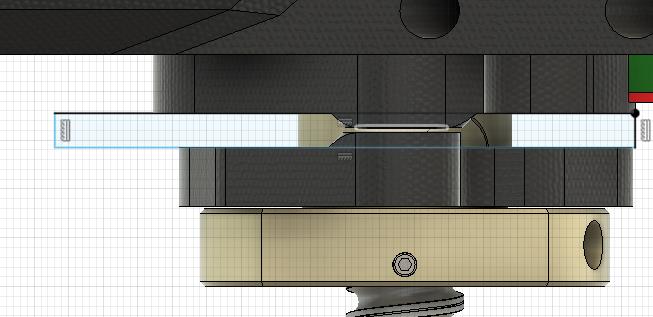
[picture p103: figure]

-Check if the is no collinsion to the wobble sytem and the SFU Nut in the free space arounds it

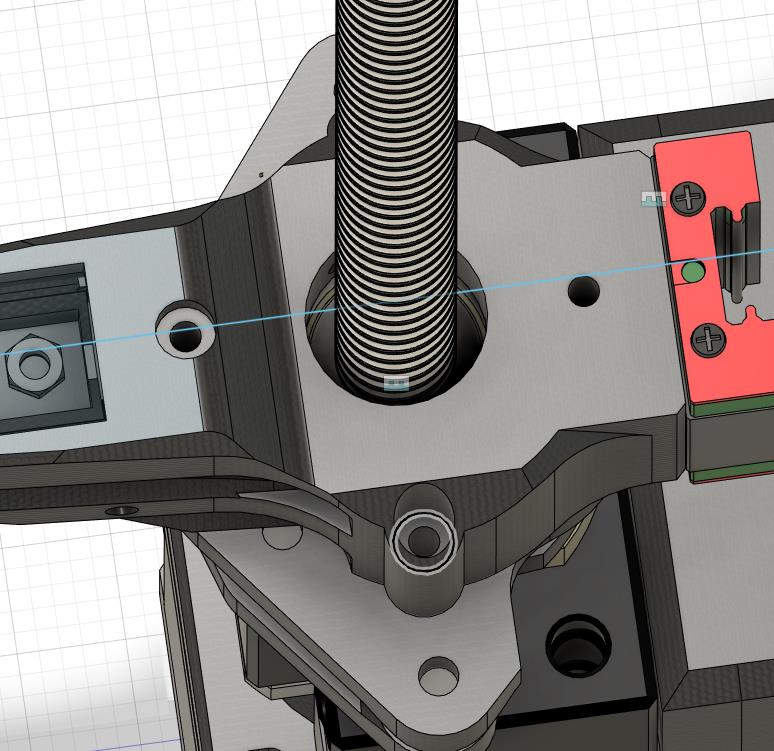
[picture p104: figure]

### 4-Last Checks :

1- Check the tightening of screws, nema etc

2- Check the alignments, in particular the RAIL / Screws

3- Hard point checks, the spindle can be rotate by hand without resistance

4- Cleanliness / lubrication checks (Rails + BS): Use a Hiwin GS04 lithium type grease or qualitative equivalent.

Page 6 sur 6

### 8-Disclaimer :

The system is designed to operate on a properly assembled Vcore. Even a slight mounting error can make it impossible to upgrade or issue during prints.

If the parts to be printed are made by the customer, check that the dimensions at the output of the printer are respected. : a bad dimension will block (+ -0.25mm) the assembly.

The machine will lose between 30 and 45mm of Z travel (depending on the screws used on the BK10s, the precision of the parts and the assembly) (32mm on the prototype), the same value for the 300, 400, 500.

This kit is an optional upgrade, intended for an informed public and having advanced experience, its assembly and / or its function and / or its quality of execution are the responsibility of the customer and are not guaranteed in public view by BRS-E. BRS-Engineering accepts no responsibility in the event of bad sourcing (bad quality and / or bad dimensions sfu), bad assembly by the customer, or bad assembly of the base Vcore.

The kit has proven its POC and POW in quality controls at BRS-E as well as at a beta test program, As is, the design works as expected

By purchasing the kit, or by having it done by BRS-Engineering, you accept the CGV as well as the previous disclaimer

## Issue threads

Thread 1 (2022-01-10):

Not nice to take someone else's designs and present it like your own.

evomotors, 2022-01-10:
This is my design: https://www.thingiverse.com/thing:4781610 it was released to public on March 02, 2021

FlorentBroise, 2022-01-11:
Hello

As courtesy has to be made to say hello

first: Your work is mentionned on my web site since the release yesterday

https://www.brs-engineering.com/Vcore3-En.html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

Second, I appologize for the late credit on the Github

I use to work 80h / week, so things can be made with delay I think it can be acceptable, I did the git release around 18h GMT today

The person which point out my design on the Hevort page never look in the site to verify his allegation, it is then falacious and fake info.

Your design has been stipped and rebuild to be more durable, I'm on this since almost  3 month and tons of fails

I added fonctions to it and it is free and available under CC BY 4.0 like yours, CC are so respected since released.

People or even you can grab it if you want.

Third: Olivier was aware of my work on it since November, He received a donation just after for the work he did and the good discussion we had

[cid:cf4ec098-ac95-4369-b368-7715c1989a1e]

4th: I just hope you weren't advertise about it by Detlev Meinhard Rackow (under his fake account) or others Ratrig minions  who "hate" my work since last summer, and want me to give them the cad under free licensing for the RR company; and take time and energy to harrass me even at Chrismas Eve, and start the same discussion few hours ago. If it is the case, I'm dissapointing in the spread of this, especially for the Hevort group which have a higher level of maturity in my POV.

5th: This solution is designed for MY upgrade mainly which concern the Vcore3 machine, Hevort is not concerned.

6th: You could simply answer my DM to clear this out, you didnt even take the opportunity and fight back right away under bad informations...

I'm still available if you want to discuss about it, I never wanted that to happenend

have a good night

[https://drive.google.com/uc?id=1ppS0cTVcHU27ylrWxZPxJkv_RZeHxkHQ]

[facebook]<https://www.facebook.com/FlorentBroiseEngineering>
        [linkedin] <https://www.linkedin.com/in/florent-broise-2a1896101/>

Florent Broise

3D-Printing engineer

 BRS Engineering

[https://cdn2.hubspot.net/hubfs/53/tools/email-signature-generator/icons/phone-icon-2x.png]
        0645326660<tel:0645326660>
[https://cdn2.hubspot.net/hubfs/53/tools/email-signature-generator/icons/email-icon-2x.png]
        ***@***.******@***.***>
[https://cdn2.hubspot.net/hubfs/53/tools/email-signature-generator/icons/link-icon-2x.png]
        www.brs-engineering.com/<https://www.brs-engineering.com/>
[https://cdn2.hubspot.net/hubfs/53/tools/email-signature-generator/icons/address-icon-2x.png]
        45 Ter rue de la résistance, 38950, St Martin Le Vinoux

________________________________
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

FlorentBroise, 2022-01-11:
For instance I saw I'm the only one to get hell about this story: Here a Ratrig beta team member with his design remixed from your which mention NO DERIVATIVE since not long ;) https://www.thingiverse.com/thing:5100367
But as Beta member he has obviously more rights than others.

here another one; https://github.com/cyborgcnc/CYBORGCNC__RRVC3MOD/tree/main/WOBBLE-RINGS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
But he obviously have not to worry

You solution is base on a 2017 Oldham coupler way before your design. As you wish to fight and I wont, I deleted the Initial release, but a new one is already here and respecting the CC licensing. Since it is not the same system at all.

FlorentBroise, 2022-03-11:
Changing you license mid course is not gonna solve the issue, CC Licenses are not revocable. And my remix of it respected the terms of if when it was under CC-BY 4.0.

Closed 2022-01-12.

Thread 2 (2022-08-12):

Why wobble rings with a two-part middle ring?

keenle, 2022-08-12:
Hi there!

Looking at your wobble rings remix https://store.brs-engineering.com/fr-us/products/decoupleur-oldham and not sure how to explain some of remix design decisions.... Could you tell:

1. Why middle ring from two pieces?
2. Why fixing bolt in the bottom ring?

Attaching this image with in-place questions:
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

Thank you!

FlorentBroise, 2022-08-13:
Hello Keenle

The m6 headless screw / or grease tip, is here to opturate the grease port of the nut, you see a small recess for the ease of adaptation

The 2 middle parts where basically made to structurally enhence the stiffness of the ring, as the pressure can be tremendous. For 300-400-500 version it can be of if using 6mm bed, and a robist 100% infill mùaterial and hase been design to last (no bending over time)

I made recently a 1 part middle ring a bit different which can sustain loads, it will be out soon

As you may know, this design in other community (Hevort) suffer a makor issue which is bending over time, loosing the spec, usage, reliability, repetability. I wanted a stiff-proof design to accomodate longevity to be use from 6mm to 12mm Alu cast bed, OR like a company ask, a 20mm granit bed (it exists yes^^).

Splitting the central ring in 2 and adding 4x 45° screws attachment has been proven to enhance the longevity under loads way over the maximum needed.

That is why

that said a mono central ring can do the Job with the proper material and the proper context.

As i manufacture it, I want to stick to only 1 design for ease of managment, so this design choice was made considering all of this!

Have a nice day

[https://drive.google.com/uc?id=1ppS0cTVcHU27ylrWxZPxJkv_RZeHxkHQ]

[facebook]<https://www.facebook.com/FlorentBroiseEngineering>
        [linkedin] <https://www.linkedin.com/in/florent-broise-2a1896101/>

Florent Broise

3D-Printing engineer

 BRS Engineering

[https://cdn2.hubspot.net/hubfs/53/tools/email-signature-generator/icons/phone-icon-2x.png]
        0645326660<tel:0645326660>
[https://cdn2.hubspot.net/hubfs/53/tools/email-signature-generator/icons/email-icon-2x.png]
        ***@***.******@***.***>
[https://cdn2.hubspot.net/hubfs/53/tools/email-signature-generator/icons/link-icon-2x.png]
        www.brs-engineering.com/<https://www.brs-engineering.com/>
[https://cdn2.hubspot.net/hubfs/53/tools/email-signature-generator/icons/address-icon-2x.png]
        45 Ter rue de la résistance, 38950, St Martin Le Vinoux

________________________________
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

FlorentBroise, 2022-09-09:
Hi there! I've uploaded a central ring update in 1 part to match ease of manufactuing, Can be use with 6mm bed without issues so far after few fatigue tests since this summer/ https://raw.githubusercontent.com/FlorentBroise/BRS-Printers-Mod/main/cad/RingUnifiedv2.step

Closed 2022-09-09.

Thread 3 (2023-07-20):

BOM-ZU2 - Clarification needed

Deynet88, 2023-07-20:
Hi Florent,

I have two questions:

1) BK10: Needed quantity should be 3 instead of 2, right?
2) BK10: With normal or angular bearings?

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

Thanks in advance.

Best regards

FlorentBroise, 2023-07-20:
Hello Deynet88

1/ Yes 3, I will correct this mistake.

2/ BK10 with angular bearings is not that easy to find as an SFU package kit, I use to buy angular bearing by myself and swap them in the BK10 housing.
Angular bearing are actually better on the theorical aspect to hold the weight and have a better reliability. That said the stock non angularat bearing behave ok too since it never exceeds their axial load limit...
If you want to be square with the principle, changing to angular bearing is a good thing

FlorentBroise, 2023-08-20:
I guess the issue has been cleared, I'm closing it ;)

Closed 2023-08-20.

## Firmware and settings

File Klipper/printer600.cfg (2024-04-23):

#=======================
# Vulcain 600 V1.3 / Klipper mod by Broise - Florent / BRS-ENGINNERING/BRS-Tech All rights reserved
#=======================
# Hardware - M8P V2.0 Board
#=======================

[save_variables]
filename: ~/printer_data/config/saved_variables.cfg

# INCLUDES
[include mainsail.cfg]
[include macros/macros-brs.cfg]
[include macros/fast_infill.cfg]

[mcu] #MANTA M8P V2
baud: 250000
serial: /dev/serial/by-id/usb-Klipper_stm32h723xx_1E002D001951313434373135-if00

#[mcu PIS] #ADXL module
#serial: /dev/serial/by-id/usb-Klipper_rp2040_E66160F423363E38-if00

[virtual_sdcard]
path: ~/printer_data/gcodes/USB1
on_error_gcode: CANCEL_PRINT

[mcu rpi] #CM4
serial: /tmp/klipper_host_mcu

[printer]
kinematics: corexy
max_velocity: 350
max_accel: 15000		
max_z_velocity: 35		
max_z_accel: 20
square_corner_velocity: 7

[temperature_sensor Manta]
sensor_type: temperature_mcu

[temperature_sensor CM4]
sensor_type: temperature_host

[idle_timeout]
gcode:
  M117 Idle timeout reached
  TURN_OFF_HEATERS
  M84
  LEDS_OFF
timeout: 999999999

[skew_correction]

[display_status]

[pause_resume]

[respond]

[force_move]
enable_force_move: True

[gcode_arcs]
resolution: 1.0

#####################################################################
# 	X/Y Stepper Settings
#####################################################################

## X Stepper on Motor1(B Motor)
[stepper_y1]
step_pin: PE6
dir_pin: !PE5
enable_pin: !PC14
microsteps: 32
rotation_distance: 40.0
full_steps_per_rotation: 200 # 1.8 Degree Stepper Motor

[tmc2209 stepper_y1]
uart_pin: PC13
interpolate: False
# TMC2226-LDO-42STH48-2504AC
run_current: 1.6
stealthchop_threshold: 0
sense_resistor: 0.110
driver_TBL: 2
driver_TOFF: 3
driver_HSTRT: 6
driver_HEND: 0

[stepper_x1]
step_pin: PE2
dir_pin: !PE1
enable_pin: !PE4
microsteps: 32
rotation_distance: 40.0
full_steps_per_rotation: 200 # 1.8 Degree Stepper Motor

[tmc2209 stepper_x1]
uart_pin: PE3
interpolate: False
# TMC2226-LDO-42STH48-2504AC
run_current: 1.6
stealthchop_threshold: 0
sense_resistor: 0.110
driver_TBL: 2
driver_TOFF: 3
driver_HSTRT: 6
driver_HEND: 0

[stepper_y]
step_pin: PB4
dir_pin: PB3
enable_pin: !PB6
microsteps: 32
rotation_distance: 40.0
endstop_pin: PF4
position_endstop: 590
position_max: 590
homing_speed: 80  #Max 100
homing_retract_dist: 5
full_steps_per_rotation: 200 # 1.8 Degree Stepper Motor

[tmc2209 stepper_y]
uart_pin: PB5
interpolate: False
# TMC2226-LDO-42STH48-2504AC
run_current: 1.6
stealthchop_threshold: 0
sense_resistor: 0.110
driver_TBL: 2
driver_TOFF: 3
driver_HSTRT: 6
driver_HEND: 0

[stepper_x]
step_pin: PG13
dir_pin: PG12
enable_pin: !PG15
microsteps: 32
rotation_distance: 40.0
endstop_pin: PF3
position_endstop: 0
position_max: 605
homing_speed: 80   #Max 100
homing_retract_dist: 5
full_steps_per_rotation: 200 # 1.8 Degree Stepper Motor

[tmc2209 stepper_x]
uart_pin: PG14
interpolate: False
# TMC2226-LDO-42STH48-2504AC
run_current: 1.6
stealthchop_threshold: 0
sense_resistor: 0.110
driver_TBL: 2
driver_TOFF: 3
driver_HSTRT: 6
driver_HEND: 0

#####################################################################
# 	Z Stepper Settings
#####################################################################

## Z0 Stepper - Front Left on MOTOR4
[stepper_z]
step_pin: PG9
dir_pin: !PD7
enable_pin: !PG11
rotation_distance: 5
full_steps_per_rotation: 200 # 1.8 Degree Stepper Motor
microsteps: 32
##  Z-position of nozzle (in mm) to z-endstop trigger point relative to print surface (Z0)
##  (+) value = endstop above Z0, (-) value = endstop below
##	Increasing position_endstop brings nozzle closer to the bed
##  After you run Z_ENDSTOP_CALIBRATE, position_endstop will be stored at the very end of your config
endstop_pin: probe:z_virtual_endstop
position_max: 576
position_min: -12
homing_speed: 6
second_homing_speed: 1
homing_retract_dist: 3

[tmc2209 stepper_z]
uart_pin: PG10
interpolate: false
stealthchop_threshold: 0
run_current: 1.3
sense_resistor: 0.110

##	Z1 Stepper - Rear Left on Motor4
[stepper_z1]
step_pin: PD4
dir_pin: !PD3
enable_pin: !PD6
rotation_distance: 5
full_steps_per_rotation: 200 # 1.8 Degree Stepper Motor
microsteps: 32

[tmc2209 stepper_z1]
uart_pin: PD5
interpolate: false
stealthchop_threshold: 0
run_current: 1.3
sense_resistor: 0.110

##	Z2 Stepper - Rear Right on Motor5
[stepper_z2]
step_pin: PC7
dir_pin: !PC8
enable_pin: !PD2
rotation_distance: 5
full_steps_per_rotation: 200 # 1.8 Degree Stepper Motor
microsteps: 32

[tmc2209 stepper_z2]
uart_pin: PC6
interpolate: false
run_current: 1.3
stealthchop_threshold: 0
sense_resistor: 0.110

#####################################################################
# 	Bed Heater
#####################################################################

[heater_bed]
heater_pin: PF5
sensor_type: ATC Semitec 104GT-2
sensor_pin: PB1
min_temp: 0
max_temp: 120
#control: pid
#pid_Kp: 64.178
#pid_Ki: 1.465
#pid_Kd: 702.752

#####################################################################
# 	Toolhead VZ
#####################################################################

## Extruder
[extruder]
step_pin: PB8
dir_pin: !PB7
enable_pin: !PE0
heater_pin: PA0
sensor_pin: PB0
microsteps: 16
full_steps_per_rotation: 200
gear_ratio: 50:10
rotation_distance: 21.977
filament_diameter: 1.750
max_extrude_only_velocity: 120 
max_extrude_cross_section: 75.0
max_extrude_only_distance: 1305 # OVERRIDE
max_extrude_only_accel: 800
nozzle_diameter: 0.6
sensor_type: PT1000 # Hot End - Thermister Type
pullup_resistor: 4700
min_extrude_temp: 180
min_temp: 0 # Hot End - Set to -100 for diagnostics / 0 for normal operations.
max_temp: 300 # OVERRIDE
pressure_advance: 0.0658
#control: pid
#pid_kp: 21.147
#pid_ki: 1.659
#pid_kd: 67.406

[tmc2209 extruder]
uart_pin: PB9
run_current: 0.707
stealthchop_threshold: 0
sense_resistor: 0.110
#driver_TBL: 1 
#driver_TOFF: 3
#driver_HSTRT: 7
#driver_HEND: 9
interpolate: False

[fan]
pin: rpi:gpio21
cycle_time: 0.002
hardware_pwm: false
max_power: 1.0
shutdown_speed: 1.0

[heater_fan toolhead_cooling_fan]
pin: PF7
max_power: 1.0
fan_speed: 1.0
shutdown_speed: 0.0
heater: extruder

#==========================
#ADXL & Resonance Setttings
#==========================

##[adxl345]
#cs_pin: PIS:gpio13
##spi_bus: spi1a
#spi_software_sclk_pin: PIS:gpio10
#spi_software_mosi_pin: PIS:gpio11
#spi_software_miso_pin: PIS:gpio12
#axes_map: x,-z,y

#[resonance_tester]
#accel_chip: adxl345 
## accel_chip: adxl345 
#probe_points:
#    300,300,30 # an example

[input_shaper]
#shaper_freq_x: 104
#shaper_type_x: mzv
#shaper_freq_y: 62.8
#shaper_type_y: mzv

#####################################################################
# 	Probe
#####################################################################

[probe]
pin: !PD8
x_offset: 10
y_offset: -10
#z_offset: 0
speed: 3
samples: 3
sample_retract_dist: 2
lift_speed: 20
samples_result: average
samples_tolerance: 0.02
samples_tolerance_retries: 5


#####################################################################
# 	Fan Control
#####################################################################

#[fan]
###	Print Cooling Fan - CNC_FAN0
#pin: PE0
#max_power: 1.0
#shutdown_speed: 1.0

#[heater_fan hotend_fan]
###	Hotend Fan - CNC_FAN1
#pin: PE5
#max_power: 1.0
#kick_start_time: 0.5
#heater: extruder
#heater_temp: 50.0
##	If you are experiencing back flow, you can reduce fan_speed
#2fan_speed: 1

#[controller_fan driver_fan]
#pin: VF5
#max_power: 1.0
#off_below: 0.10
#fan_speed: 1.0
#shutdown_speed: 1.0
#cycle_time: 0.0001
#idle_timeout: 60
#idle_speed: 1.0
#tachometer_pin: PA6
#tachometer_poll_interval: 0.0005
#stepper: stepper_x, stepper_y


#####################################################################
# 	LED Control
#####################################################################

[neopixel led_status]
pin: PD15
#   The pin connected to the neopixel. This parameter must be
#   provided.
chain_count: 41
#   The number of Neopixel chips that are "daisy chained" to the
#   provided pin. The default is 1 (which indicates only a single
#   Neopixel is connected to the pin).
color_order: GRB
#   Set the pixel order required by the LED hardware. Options are GRB,
#   RGB, GRBW, or RGBW. The default is GRB.
initial_RED: 1.0
initial_GREEN: 1.0
initial_BLUE: 1.0
#initial_WHITE: 0.0
#   Sets the initial LED color of the Neopixel. Each value should be
#   between 0.0 and 1.0. The WHITE option is only available on RGBW
#   LEDs. The default for each color is 0.

#####################################################################
# 	Homing and Gantry Adjustment Routines
#####################################################################

[bed_mesh]
speed: 200
horizontal_move_z: 15
mesh_min: 20,20 # OVERRIDE
mesh_max:550,560 # OVERRIDE
probe_count: 22,22
fade_start: 1.0
fade_end: 10.0
mesh_pps: 2,2
algorithm: bicubic
bicubic_tension: .2

[z_tilt]

z_positions:
        0,0
        300,600
        600,0
points:
        20,20
        300,560
        540,20
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

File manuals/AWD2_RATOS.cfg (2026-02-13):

#####################################################################
# 	X/Y Stepper Settings
#####################################################################

[stepper_y1]
step_pin: PF13
dir_pin: !PF12
enable_pin: !PF14
microsteps: 16
rotation_distance: 40.0
full_steps_per_rotation: 200 # 1.8 Degree Stepper Motor

[tmc2209 stepper_y1]
uart_pin: PC4
interpolate: False
# TMC2226-LDO-42STH48-2504AC
run_current: 1.6
stealthchop_threshold: 0
sense_resistor: 0.110
driver_TBL: 2
driver_TOFF: 3
driver_HSTRT: 6
driver_HEND: 0

[stepper_x1]
step_pin: PG0
dir_pin: !PG1
enable_pin: !PF15
microsteps: 16
rotation_distance: 40.0
full_steps_per_rotation: 200 # 1.8 Degree Stepper Motor

[tmc2209 stepper_x1]
uart_pin: PD11
interpolate: False
# TMC2226-LDO-42STH48-2504AC
run_current: 1.6
stealthchop_threshold: 0
sense_resistor: 0.110
driver_TBL: 2
driver_TOFF: 3
driver_HSTRT: 6
driver_HEND: 0

[stepper_y]
step_pin: PG4
dir_pin: PC1
enable_pin: !PA0
microsteps: 16
rotation_distance: 40.0
endstop_pin: PG9
position_min: -2.35
position_max: 530
position_endstop: -2.35
homing_speed: 80  #Max 100
homing_retract_dist: 5
full_steps_per_rotation: 200 # 1.8 Degree Stepper Motor

[tmc2209 stepper_y]
uart_pin: PC7
interpolate: False
# TMC2226-LDO-42STH48-2504AC
run_current: 1.6
stealthchop_threshold: 0
sense_resistor: 0.110
driver_TBL: 2
driver_TOFF: 3
driver_HSTRT: 6
driver_HEND: 0

[stepper_x]
step_pin: PF9
dir_pin: PF10
enable_pin: !PG2
microsteps: 16
rotation_distance: 40.0
#endstop_pin: ***************
position_min: -59.6
position_max: 557.8
position_endstop: -59.6
homing_speed: 80   #Max 100
homing_retract_dist: 5
full_steps_per_rotation: 200 # 1.8 Degree Stepper Motor

[tmc2209 stepper_x]
uart_pin: PF2
interpolate: False
# TMC2226-LDO-42STH48-2504AC
run_current: 1.6
stealthchop_threshold: 0
sense_resistor: 0.110
driver_TBL: 2
driver_TOFF: 3
driver_HSTRT: 6
driver_HEND: 0

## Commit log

2023-08-19 Create Plates-Enclosures .md
2023-08-19 Rename Plates-Enclosures .md to Plates-Enclosures.md
2024-03-22 Update and rename klippersetupdraft.md to klippersetup.md
2026-02-13 Update and rename AWD2.cfg to AWD2_RATOS.cfg
    [AWD2_RATOS.cfg]

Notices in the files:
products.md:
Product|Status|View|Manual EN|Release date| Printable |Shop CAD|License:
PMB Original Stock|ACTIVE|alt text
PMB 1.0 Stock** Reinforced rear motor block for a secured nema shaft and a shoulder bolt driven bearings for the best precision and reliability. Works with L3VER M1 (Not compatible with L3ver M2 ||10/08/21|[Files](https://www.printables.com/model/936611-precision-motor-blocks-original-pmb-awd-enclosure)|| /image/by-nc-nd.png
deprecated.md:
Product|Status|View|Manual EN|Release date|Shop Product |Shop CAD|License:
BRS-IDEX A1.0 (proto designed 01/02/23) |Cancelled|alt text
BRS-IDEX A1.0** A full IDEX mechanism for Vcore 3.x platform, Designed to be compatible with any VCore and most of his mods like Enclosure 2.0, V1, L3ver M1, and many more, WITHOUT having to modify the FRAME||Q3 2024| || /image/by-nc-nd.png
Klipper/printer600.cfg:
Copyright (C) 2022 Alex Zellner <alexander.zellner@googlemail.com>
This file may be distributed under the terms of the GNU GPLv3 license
